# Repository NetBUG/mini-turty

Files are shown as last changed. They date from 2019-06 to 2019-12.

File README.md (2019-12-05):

# mini-turty

ROS package for the Mini-Turty robot.

Original product website: https://www.rhoeby.com/product/mini-turty
    
The Mini-Turty Robot from Rhoeby Dynamics represents a new level of value and functionality in a ROS navigation-capable robot. Designed with the lowest cost and complete user serviceability in mind, this robot is providing greatly improved access to advanced robotics navigation and much more!

## Hardware
The repository contains a [sample platform](mini_turty3/hw/lasercut) designed to be made with laser cutting. 
The base is cut out of 3mm birch plywood with principal strength direction oriented transversely (i.e. robot does not bend between the wheels).
Any other elements are cut out of 3 or 4mm acrylic sheet of any color. Motor holders are not optimal and will be improved soon to provide active suspension.
Unfortunately, the front navigation module (can be seen on sheets as a rectangle of 120x85 mm) was made long ago and design was lost. It contains:
 - Raspberry Pi 3 with heatsink, mounted on 4xM2 screws on the bottom sheet;
 - Neato xv11 lidar, mounted on upper sheet (which is elevated with 30mm M3 screws and pipe-like stands)
 - Raspberry Pi 3 extension made on a prototyping board with PLS connectors, providing connections to
  * lidar through on-board UART (serial kernel logging was disabled)
  * lidar motor power through a low-power SOT23 MOSFET
  * stepper driver outputs
  * I2C connector for  sensors (used for IMU)
  * 4xGPIO pins

The following external components have been used and fit on the base:
 - [18650-sized battery holder](https://www.thingiverse.com/thing:456900)
 - [LV8729 drivers](https://www.aliexpress.com/item/32808950520.html)
 - 2xNEMA17 stepper motors with Makeblocks wheels and wheel hubs
 - A [ball stand](https://pandao.ru/product/233c3d45-5e80-4f82-84e4-e2d594d67a44)

The following components have been fit on the upper board
 - A stepdown module using XL6009 chip
 - An [IMU](https://amperka.ru/product/troyka-imu-10-dof)
 - An IR receiver
 - [Power controller board](mini_turty3/hw/controller)

Drawings use the following coloring convention:
 - black means the lines that have to be cut
 - red means lines denoting mounted parts dimensions and should be omitted when cutting (originally it was used as pale dashed line)
 - yellow originally denoted contours filled with yellow and was used in engraving mode to provide submerged areas to hide PCBs or screen frame

## Things You Can Do With Your Mini-Turty Robot

There are many things you can do with your Mini-Turty robot, including:

- Basics: ROS learning
- Teleop: robot remote control
- Map Building: make maps of your home or office for the robot to use
- Navigation: the robot moves autonomously around your home or office
- Tele-Viewing: see what your robot sees, even from another room*
- Frontier Exploration: the robot autonomously explores unknown terrain*
- Computer Vision: Mini-Turty recognizes objects in its environment*

*Coming soon, to a robot near you!

Available in kit form*, or fully assembled and ready to go. Either way, Mini-Turty provides endless hours of educational fun and represents the ideal platform for learning the Robot Operating System.

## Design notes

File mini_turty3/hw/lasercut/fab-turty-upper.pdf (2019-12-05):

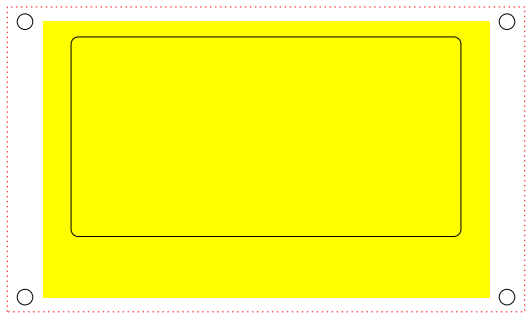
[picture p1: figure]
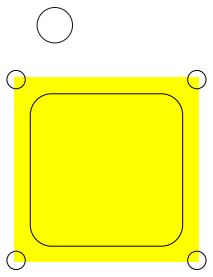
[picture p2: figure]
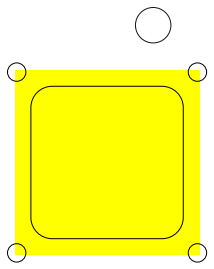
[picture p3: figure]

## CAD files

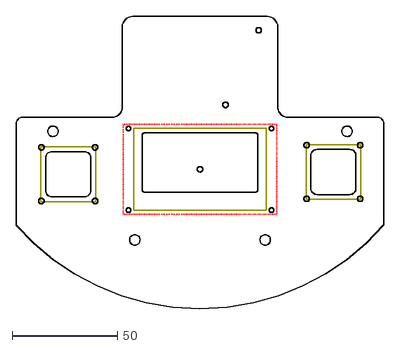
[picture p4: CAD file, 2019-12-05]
mini_turty3/hw/lasercut/fab-turty-upper.dxf
175.0 x 139.0

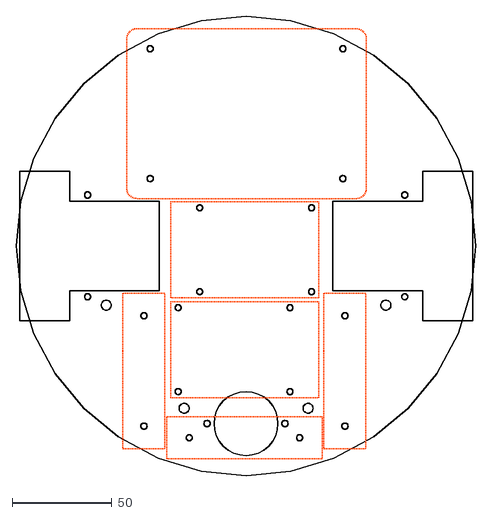
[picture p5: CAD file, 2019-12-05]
mini_turty3/hw/lasercut/fab-turty-base.dxf
230.0 x 230.0

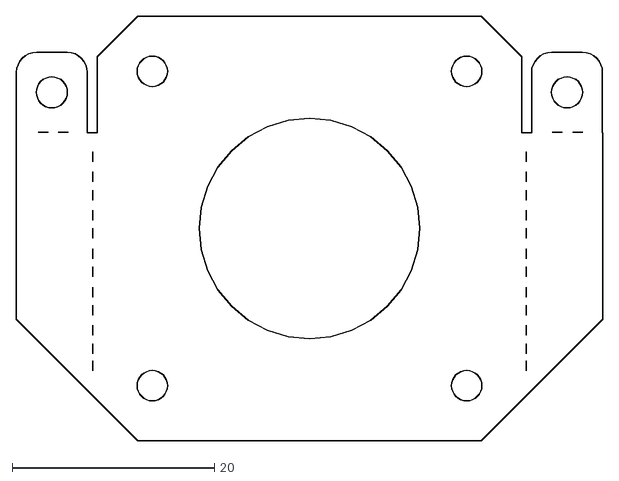
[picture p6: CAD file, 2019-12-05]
mini_turty3/hw/lasercut/fab-turty-motor-holder-x2.dxf
58.0 x 42.0

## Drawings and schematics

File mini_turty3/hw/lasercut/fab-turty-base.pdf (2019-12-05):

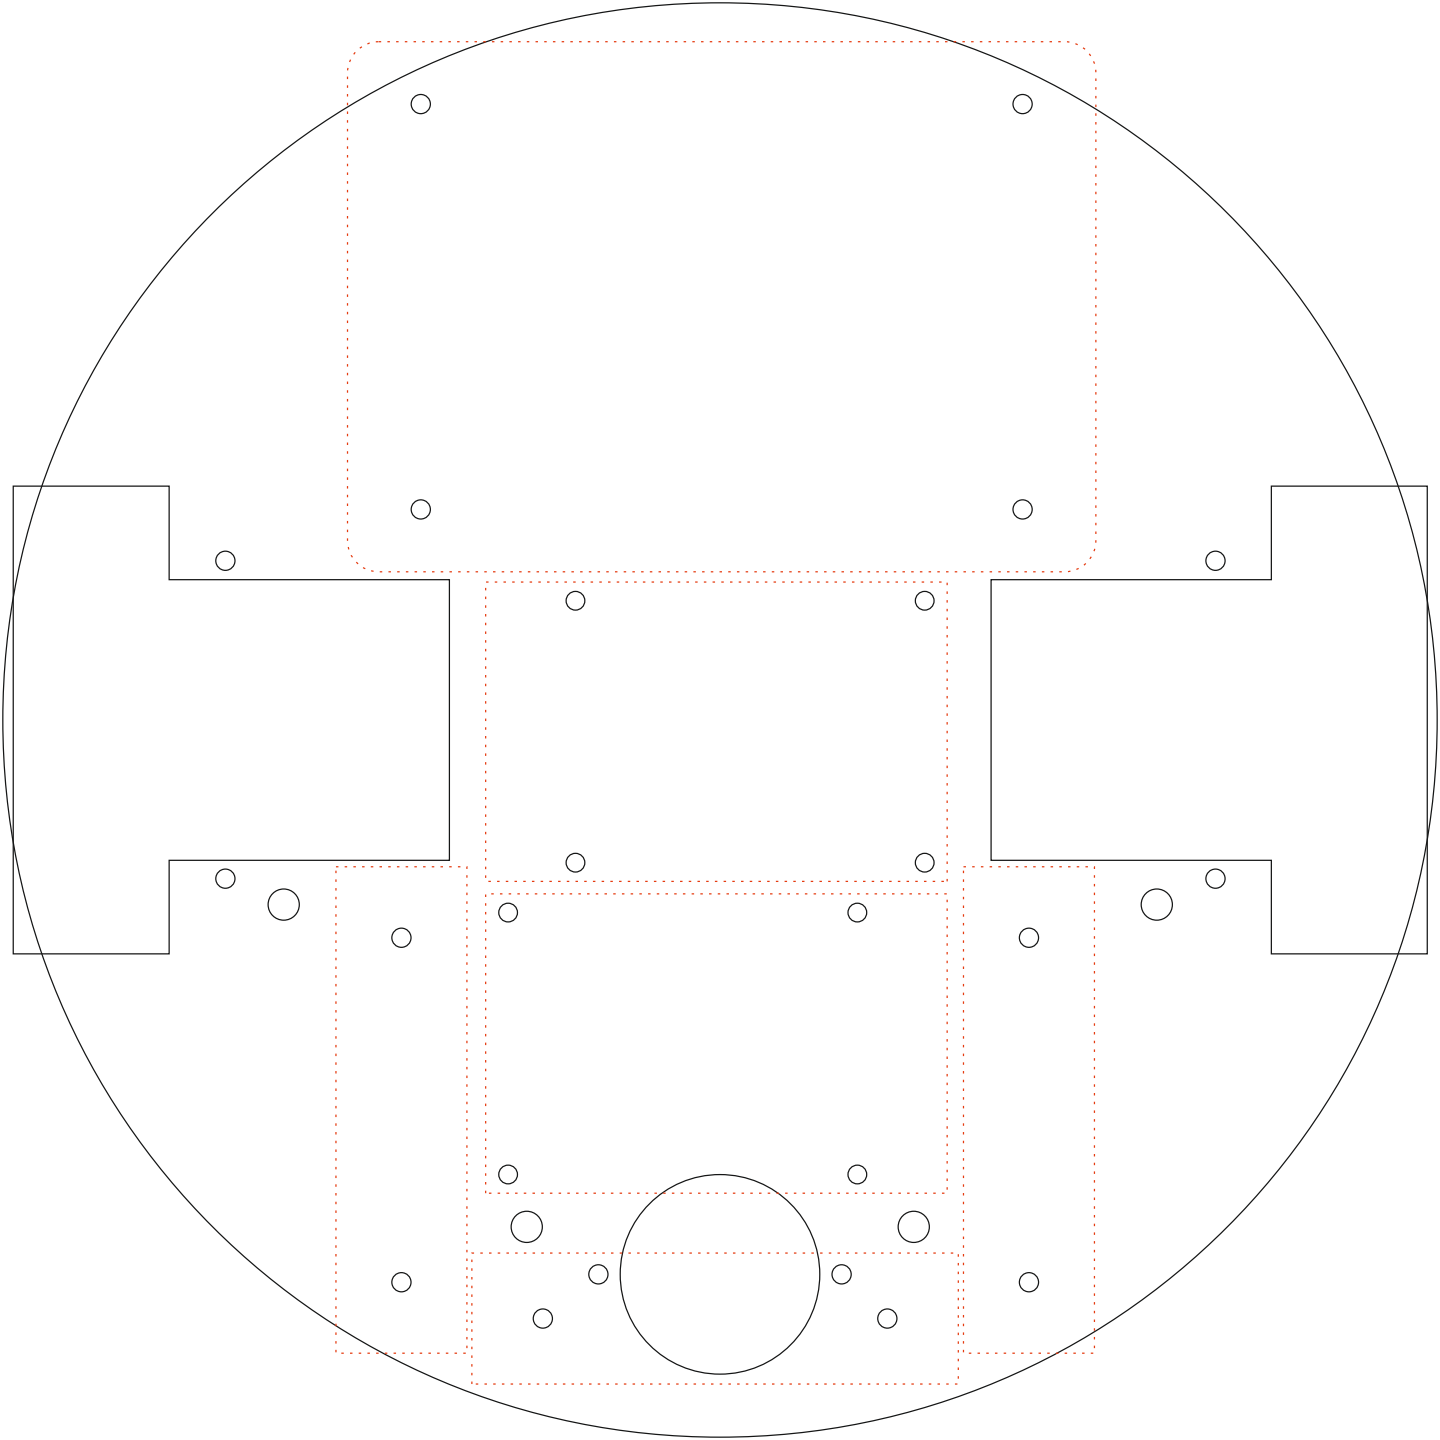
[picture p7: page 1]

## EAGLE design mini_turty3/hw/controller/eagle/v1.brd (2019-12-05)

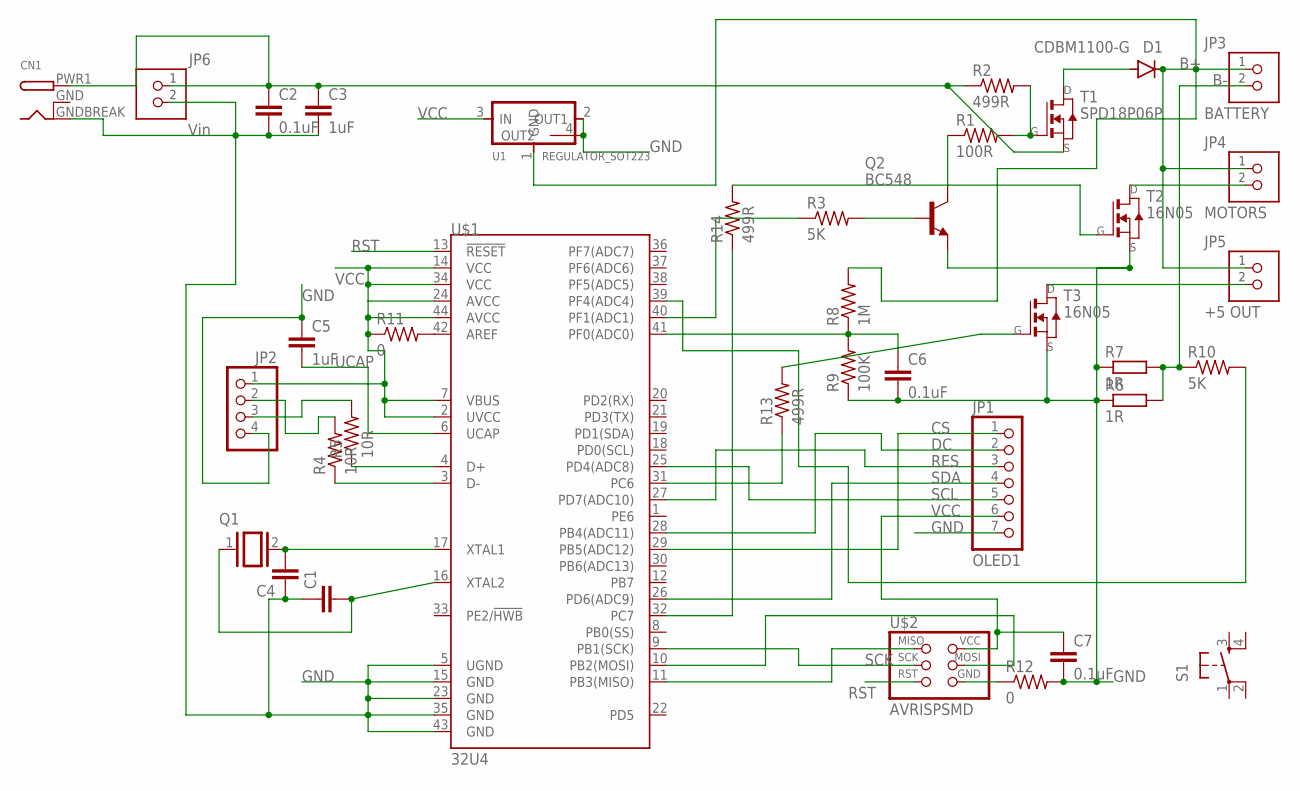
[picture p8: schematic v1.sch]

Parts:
C1, C4: C-EUC1206; C1206
C2, C6, C7: 0.1uF; C1206
C3, C5: 1uF; C1206
CN1: DCBARRELSMT; DCJACK_2MM_SMT
D1: CDBM1100-G; MINI-SMA
JP1: OLED1; 1X07
JP2: PINHD-1X4; 1X04
JP3: BATTERY; ED555DS-2DS
JP4: MOTORS; ED555DS-2DS
JP5: +5 OUT; ED555DS-2DS
JP6: Vin; ED555DS-2DS
Q1: XTAL/S; QS
Q2: BC548; TO92-EBC
R1: 100R; M1206
R2, R13, R14: 499R; M1206
R3, R10: 5K; M1206
R4, R5: 10R; M1206
R6, R7: 1R; R6332W
R8: 1M; M1206
R9: 100K; M1206
R11, R12: 0; M1206
S1: 6MM_SWITCH6MM_SWITCH; 6MM_SWITCH
T1: SPD18P06P; TO252
T2, T3: 16N05; TO252
U1: REGULATOR_SOT223; SOT223
U$1: 32U4; TQFP44
U$2: AVRISPSMD; 2X03SMD

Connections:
B+: D1.KATHODE, JP3.1, JP4.1, JP5.1, R8.2, U1.1 (GND)
B-: JP3.2, R6.2, R7.2, R10.1
CS: JP1.1, U$1.29 (PB5(ADC12))
DC: JP1.2, U$1.28 (PB4(ADC11))
GND: C1.1, C2.2, C3.2, C4.1, C5.1, C6.2, C7.2, CN1.GNDBREAK (GND), JP1.7, JP2.4, JP6.2, Q2.E, R6.1, R7.1, R9.1, R12.2, T2.2 (S), T3.2 (S), U1.2 (OUT1), U1.4 (OUT2), U$1.5 (UGND), U$1.15 (GND), U$1.23 (GND), U$1.35 (GND), U$1.43 (GND)
GNDBREAK: CN1.GND (GNDBREAK)
MISO: U$1.11 (PB3(MISO)), U$2.1 (MISO)
MOSI: U$1.10 (PB2(MOSI)), U$2.4 (MOSI)
unnamed: C4.2, Q1.2, U$1.17 (XTAL1)
unnamed: R11.2, U$1.42 (AREF)
unnamed: R3.1, U$1.40 (PF1(ADC1))
unnamed: R12.1, U$2.6 (GND)
unnamed: C1.2, Q1.1, U$1.16 (XTAL2)
unnamed: JP5.2, T3.3 (D)
unnamed: JP4.2, T2.3 (D)
unnamed: R14.1, U$1.32 (PC7)
unnamed: D1.ANODE, T1.3 (D)
unnamed: R1.2, R2.2, T1.1 (G)
unnamed: Q2.C, R1.1
unnamed: Q2.B, R3.2
unnamed: R13.1, U$1.31 (PC6)
unnamed: C6.1, R8.1, R9.2, U$1.41 (PF0(ADC0))
unnamed: R10.2, U$1.39 (PF4(ADC4))
unnamed: JP2.3, R5.2
unnamed: R5.1, U$1.4 (D+)
unnamed: R4.1, U$1.3 (D-)
unnamed: JP2.2, R4.2
unnamed: R14.2, T2.1 (G)
unnamed: R13.2, T3.1 (G)
RES: JP1.3, U$1.27 (PD7(ADC10))
RST: U$1.13 (!RESET), U$2.5 (RST)
SCK: U$1.9 (PB1(SCK)), U$2.3 (SCK)
SCL: JP1.5, U$1.25 (PD4(ADC8))
SDA: JP1.4, U$1.26 (PD6(ADC9))
UCAP: C5.2, U$1.6 (UCAP)
VCC: C7.1, JP1.6, JP2.1, R11.1, U1.3 (IN), U$1.2 (UVCC), U$1.7 (VBUS), U$1.14 (VCC), U$1.24 (AVCC), U$1.34 (VCC), U$1.44 (AVCC), U$2.2 (VCC)
VIN: C2.1, C3.1, CN1.PWR1 (PWR), JP6.1, R2.1, T1.2 (S)

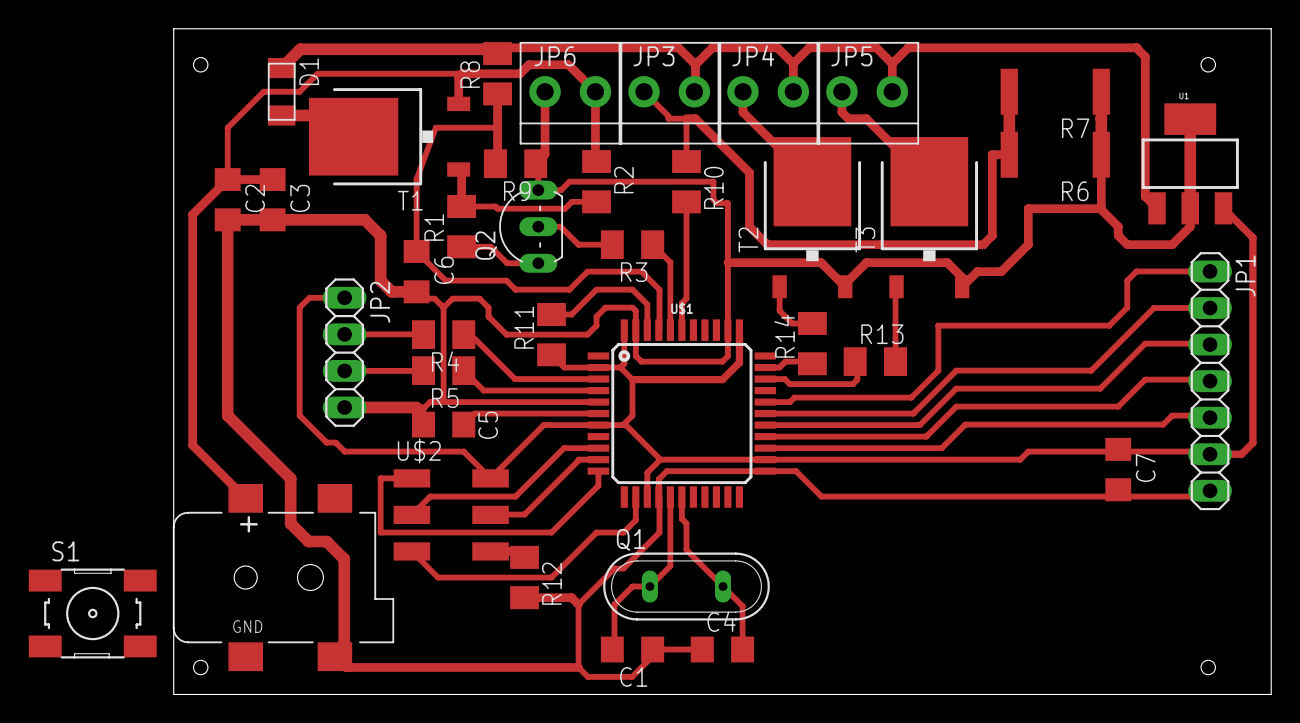
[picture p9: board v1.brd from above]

Board: 2 copper layers, 76.2 x 46.2 mm, 38 parts (0 on the bottom side), 36 nets.

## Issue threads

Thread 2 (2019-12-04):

Олег, выложи механику

kotenev, 2019-12-04:
Приветствую. По договорённости в чате "ros meetup 2019" создал этот issue :-)

NetBUG, 2019-12-05:
Вспомнил, что у меня есть удалённый доступ))
Выложил в ветку `hw`, в подкаталог `mini-turty3/hw`.
Фотографии, чертёж модуля с RPi и лидаром, полноценную прошивку BMS выложу, когда приеду в Москву.
Привод с ременной передачей и подвеской, видимо, в январе.

Closed 2019-12-05.

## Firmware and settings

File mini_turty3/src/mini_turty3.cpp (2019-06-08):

#include <stdio.h>
#include <stdlib.h>
#include <signal.h>
#include <string>

#include <fcntl.h>
#include <termios.h>
#include <sys/select.h>

#include "pigpiod_if2.h"
#include "ros/ros.h"
#include <ros/console.h>
#include "nav_msgs/Odometry.h"
#include "tf/transform_broadcaster.h"

/*
NOTE - Must start 'pigpiod' daemon first:
  sudo pigpiod
*/

// options
#define MINI_USE_CONSOLE 1

// GPIO pin assignments
#define GPIO_SLEEP 16
#define GPIO_STEP1 19
#define GPIO_DIR1  26
#define GPIO_STEP0 13
#define GPIO_DIR0  20

#define MOTOR_SPEED_SLEW_SIZE 0.45 // rate of change of motor speed (in m/s)
#define MAX_DEFAULT_SPEED 16

typedef enum DIFFDRIVE_MOTOR
{
  DIFFDRIVE_MOTOR_LEFT,
  DIFFDRIVE_MOTOR_RIGHT,
  DIFFDRIVE_MOTOR_MAX
} DIFFDRIVE_MOTOR;

typedef struct Motor_t {
  double currentSpeed;
  double targetSpeed;
} Motor_t;

class MiniTurtyBase
{
  public:
    MiniTurtyBase(int the_pi, float max_speed);
    virtual ~MiniTurtyBase() {};

    void setEnableOdomTransform(const bool enabled);
    void setCmdVelTopic(const std::string topic_name);
    void setMotorSpeed(DIFFDRIVE_MOTOR motor_num, double speed);

  protected:
    void cmdVelCallback(const geometry_msgs::Twist::ConstPtr& twist);
    void timerCallback(const ros::TimerEvent&);
    void updateMotorControl(DIFFDRIVE_MOTOR motor_num);
    void publishOdom(const double vx, const double vth);

  private:
    int pi;
    float max_speed;
    ros::NodeHandle node;
    ros::Subscriber cmd_vel_sub;
    ros::Timer timer;
    Motor_t motors[DIFFDRIVE_MOTOR_MAX];
    tf::TransformBroadcaster odom_broadcaster;
    bool odomTransformEnabled;
};

int init_gpio(void);

#if MINI_USE_CONSOLE
void consoleSetTerminalMode(void);
char processConsole(MiniTurtyBase *mini);
#else
void sig_handler(int s);
static bool got_ctrl_c = false;
#endif

//////////////////////////////////////////////////////////////////////////////

int main(int argc, char *argv[])
{
  int pi;
  
  ROS_WARN("Hello!\n");

  pi = init_gpio();
  if(pi) {
    ROS_ERROR("Error initializing pigpio!\n");
    return pi;
  }

  ros::init(argc, argv, "mini_turty");

#if MINI_USE_CONSOLE
  consoleSetTerminalMode();
#else
  signal(SIGINT, sig_handler);
#endif

  ros::NodeHandle private_node_handle_("~");
  ros::Rate loop_rate(10);

  int enable_odom_transform;
  float max_speed;
  private_node_handle_.param("enable_odom_transform", enable_odom_transform, int(1));
  private_node_handle_.param("max_speed", max_speed, float(MAX_DEFAULT_SPEED));

  MiniTurtyBase mini(pi, max_speed);
  mini.setCmdVelTopic("cmd_vel");
  mini.setEnableOdomTransform(enable_odom_transform);
  mini.setEnableOdomTransform(enable_odom_transform);

  while (ros::ok()) 
  {
#if MINI_USE_CONSOLE
    if(processConsole(&mini) == 'q') {
      ROS_WARN("Got 'q'");
      break;
    }
#else
    if (got_ctrl_c) {
      ROS_WARN("Got Ctrl-C");
      break;
    }
#endif

    ros::spinOnce();
    loop_rate.sleep();
  }

  // set SLEEP (active low)
  gpio_write(pi, GPIO_SLEEP, 1);
  
  pigpio_stop(pi);

  ROS_WARN("Exiting.");

  exit(0);
}

/////////////////////////////////////////////////////////////////////////

/*---------------------------------------------------------------------
 *
 *---------------------------------------------------------------------*/
MiniTurtyBase::MiniTurtyBase(int the_pi, float max_speed)
{
  pi = the_pi;

  motors[DIFFDRIVE_MOTOR_LEFT].currentSpeed = 0;
  motors[DIFFDRIVE_MOTOR_RIGHT].currentSpeed = 0;
  motors[DIFFDRIVE_MOTOR_LEFT].targetSpeed = 0;
  motors[DIFFDRIVE_MOTOR_RIGHT].targetSpeed = 0;

  timer = node.createTimer(ros::Duration(0.05), &MiniTurtyBase::timerCallback, this);
}

/*---------------------------------------------------------------------
 *
 *---------------------------------------------------------------------*/
void MiniTurtyBase::timerCallback(const ros::TimerEvent&)
{
  double vx;
  double vth;
  
  updateMotorControl(DIFFDRIVE_MOTOR_LEFT);
  updateMotorControl(DIFFDRIVE_MOTOR_RIGHT);

  vx = (motors[DIFFDRIVE_MOTOR_RIGHT].currentSpeed + 
        motors[DIFFDRIVE_MOTOR_LEFT].currentSpeed) / 2;
//  vth = (motors[DIFFDRIVE_MOTOR_RIGHT].currentSpeed - 
//         motors[DIFFDRIVE_MOTOR_LEFT].currentSpeed) * 8.25;
//  vth = (motors[DIFFDRIVE_MOTOR_RIGHT].currentSpeed - 
//         motors[DIFFDRIVE_MOTOR_LEFT].currentSpeed) * 4;
  vth = (motors[DIFFDRIVE_MOTOR_RIGHT].currentSpeed - 
         motors[DIFFDRIVE_MOTOR_LEFT].currentSpeed) * 8;

  // TODO: add a second param to control this rather than hijacking odom *transform* enable
  // don't publish odom when running hector!
  if(odomTransformEnabled)
    publishOdom(vx, vth);
}

/*---------------------------------------------------------------------
 *
 *---------------------------------------------------------------------*/
void MiniTurtyBase::updateMotorControl(DIFFDRIVE_MOTOR motor_num)
{
  double currentSpeed = motors[motor_num].currentSpeed;
  double targetSpeed = motors[motor_num].targetSpeed;
  
  if(currentSpeed == targetSpeed) return;

  // slew the current speed toward the target speed
  if(currentSpeed < targetSpeed) {
    if(currentSpeed+MOTOR_SPEED_SLEW_SIZE > targetSpeed)
      currentSpeed = targetSpeed;
    else
      currentSpeed += MOTOR_SPEED_SLEW_SIZE;
  }
  else if (currentSpeed > targetSpeed) {
    if(currentSpeed-MOTOR_SPEED_SLEW_SIZE < targetSpeed)
      currentSpeed = targetSpeed;
    else
      currentSpeed -= MOTOR_SPEED_SLEW_SIZE;
  }

  // write the current speed and direction to the motor control
  switch(motor_num) 
  {
  case DIFFDRIVE_MOTOR_LEFT:
    if(currentSpeed < 0) 
      gpio_write(pi, GPIO_DIR1, 0); // set DIRECTION
    else
      gpio_write(pi, GPIO_DIR1, 1);
//    hardware_PWM(pi, GPIO_STEP1, abs((int16_t)(currentSpeed*1000.0)), 500000);
    hardware_PWM(pi, GPIO_STEP1, abs((int16_t)(currentSpeed*2000.0)), 500000);
    break;
  case DIFFDRIVE_MOTOR_RIGHT:
    if(currentSpeed < 0) 
      gpio_write(pi, GPIO_DIR0, 1); // set DIRECTION
    else
      gpio_write(pi, GPIO_DIR0, 0);
//    hardware_PWM(pi, GPIO_STEP0, abs((int16_t)(currentSpeed*1000.0)), 500000);
    hardware_PWM(pi, GPIO_STEP0, abs((int16_t)(currentSpeed*2000.0)), 500000);
    break;
  }

  motors[motor_num].currentSpeed = currentSpeed;

  // set/reset the SLEEP of the motor control
#if 0
  if(abs(motors[DIFFDRIVE_MOTOR_LEFT].currentSpeed) < MOTOR_SPEED_SLEW_SIZE && 
     abs(motors[DIFFDRIVE_MOTOR_RIGHT].currentSpeed) < MOTOR_SPEED_SLEW_SIZE)
#else
  if(motors[DIFFDRIVE_MOTOR_LEFT].currentSpeed == 0 && 
     motors[DIFFDRIVE_MOTOR_RIGHT].currentSpeed == 0)
#endif
    gpio_write(pi, GPIO_SLEEP, 1); // set SLEEP (active low)
  else
    gpio_write(pi, GPIO_SLEEP, 0);

#if 0
  ROS_WARN("Motor: %d, Current speed: %f, Target speed: %f", 
           motor_num, currentSpeed, targetSpeed);
#endif
}

// JJ - provide odom transform
#if 1
/*----------------------------------------------------------
 * setEnableOdomTransform() - enable the odom transform
 *--------------------------------------------------------*/
void MiniTurtyBase::setEnableOdomTransform(const bool enabled)
{
  odomTransformEnabled = enabled;
}
#endif

/*----------------------------------------------------------
 * publishOdom() - publish odom data 
 *--------------------------------------------------------*/
void MiniTurtyBase::publishOdom(const double vx, const double vth)
{
  double vy = 0;
  static double x = 0;
  static double y = 0;
  static double th = 0;
  ros::Time current_time = ros::Time::now();
  static ros::Time last_time = current_time;
  static ros::Publisher odom_pub = node.advertise<nav_msgs::Odometry>("odom", 50);

#if 1
  ROS_INFO("odom vx: %f, vy: %f, vth: %f\r", vx, vy, vth);
//  printf("odom vx: %f, vy: %f, vth: %f\n", vx, vy, vth);
#endif

  // compute odometry in a typical way given the velocities of the robot
  double dt = (current_time - last_time).toSec();
  double delta_x = (vx * cos(th) - vy * sin(th)) * dt;
  double delta_y = (vx * sin(th) + vy * cos(th)) * dt;
  double delta_th = vth * dt;

  // integrate to track position
  x += delta_x;
  y += delta_y;
  th += delta_th;

  // since all odometry is 6DOF we'll need a quaternion created from yaw
  geometry_msgs::Quaternion odom_quat = tf::createQuaternionMsgFromYaw(th);

  // send the odom-->base_footprint transform: only if NOT using robot_pose_ekf!
  geometry_msgs::TransformStamped odom_trans;
  odom_trans.header.stamp = current_time;
//    odom_trans.header.frame_id = "odom_combined";
  odom_trans.header.frame_id = "odom";
//    odom_trans.child_frame_id = "base_link";
  odom_trans.child_frame_id = "base_footprint";
  odom_trans.transform.translation.x = x;
  odom_trans.transform.translation.y = y;
  odom_trans.transform.translation.z = 0.0;
  odom_trans.transform.rotation = odom_quat;
  odom_broadcaster.sendTransform(odom_trans);
#if 0
  ROS_INFO("odom x: %f, y: %f, z-rot: %f", x, y, th);
#endif

  // publish the odometry message
  nav_msgs::Odometry odom;
  odom.header.stamp = current_time;
//  odom.header.frame_id = "odom_combined";
  odom.header.frame_id = "odom";
  odom.child_frame_id = "base_footprint";

  // set the position and orientation
  odom.pose.pose.position.x = x;
  odom.pose.pose.position.y = y;
  odom.pose.pose.position.z = 0.0;
  odom.pose.pose.orientation = odom_quat;

  // TODO: these were repurposed from nxt_ros:: base_odometry.py, check the validity
  odom.pose.covariance[0] = 0.00001;    // x - are all these correct?
  odom.pose.covariance[7] = 0.00001;    // y
  odom.pose.covariance[14] = 10;    // z (set high because robot does not move up/down?)
  odom.pose.covariance[21] = 1;   // rot x
  odom.pose.covariance[28] = 1;   // rot y
  odom.pose.covariance[35] = 1;   // rot z

  // set the velocity
  odom.twist.twist.linear.x = vx;
  odom.twist.twist.linear.y = vy;
  odom.twist.twist.angular.z = vth;

  last_time = current_time;

  // publish the odom message
  odom_pub.publish(odom);
}

/*----------------------------------------------------------
 * setCmdVelTopic() - set the cmd_vel topic name 
 *--------------------------------------------------------*/
void MiniTurtyBase::setCmdVelTopic(const std::string topic_name)
{
  cmd_vel_sub = node.subscribe(topic_name, 100, &MiniTurtyBase::cmdVelCallback, this);
}

/*----------------------------------------------------------
 * cmdVelCallback()
 *--------------------------------------------------------*/
void MiniTurtyBase::cmdVelCallback(const geometry_msgs::Twist::ConstPtr& twist)
{
//  motors[DIFFDRIVE_MOTOR_LEFT].targetSpeed = twist->linear.x-twist->angular.z;
//  motors[DIFFDRIVE_MOTOR_RIGHT].targetSpeed = twist->linear.x+twist->angular.z;
//  motors[DIFFDRIVE_MOTOR_LEFT].targetSpeed = twist->linear.x-(twist->angular.z/8.25);
//  motors[DIFFDRIVE_MOTOR_RIGHT].targetSpeed = twist->linear.x+(twist->angular.z/8.25);
  motors[DIFFDRIVE_MOTOR_LEFT].targetSpeed = twist->linear.x-(twist->angular.z/16);
  motors[DIFFDRIVE_MOTOR_RIGHT].targetSpeed = twist->linear.x+(twist->angular.z/16);

#if 1
  ROS_WARN("twist linear.x: %f, y: %f, angular.z: %f\r", 
            twist->linear.x, twist->linear.y, twist->angular.z);  
#endif
}

void MiniTurtyBase::setMotorSpeed(DIFFDRIVE_MOTOR motor_num, double speed)
{
  motors[motor_num].targetSpeed = speed;
}

/////////////////////////////////////////////////////////////////////////

#if !MINI_USE_CONSOLE
void sig_handler(int s)
{
  if (s == 2) {
    got_ctrl_c = true; 
  }
}
#endif

int init_gpio(void)
{
  int pi = pigpio_start(NULL, NULL);
  if (pi < 0) goto error;

  set_mode(pi, GPIO_SLEEP, PI_OUTPUT);
  set_mode(pi, GPIO_DIR0, PI_OUTPUT);
  set_mode(pi, GPIO_DIR1, PI_OUTPUT);
  set_mode(pi, GPIO_STEP0, PI_OUTPUT);
  set_mode(pi, GPIO_STEP1, PI_OUTPUT);

error:
  return pi;
}

/*---------------------------------------------------------------
 * console functions 
 *-------------------------------------------------------------*/

#if MINI_USE_CONSOLE
struct termios orig_termios;

void consoleResetTerminalMode();
int consoleKbHit();
int consoleGetCh();

static bool started = true;
static double left_motor_speed = 0;
static double right_motor_speed = 0;

char processConsole(MiniTurtyBase *mini)
{
  char kbd_ch = 0;
  int i;
// JJ - add theta trim command
#if 0
  static int thetaTrim = 0;
#endif

  if (consoleKbHit())
  {
    kbd_ch = consoleGetCh();
    
    switch (kbd_ch)
    {
    case 'b':
      if (left_motor_speed > 0 && left_motor_speed < 4) left_motor_speed = 4;
      if (right_motor_speed > 0 && right_motor_speed < 4) right_motor_speed = 4;
      left_motor_speed -= 4;
      right_motor_speed -= 4;
      mini->setMotorSpeed(DIFFDRIVE_MOTOR_LEFT, left_motor_speed);
      mini->setMotorSpeed(DIFFDRIVE_MOTOR_RIGHT, right_motor_speed);
      ROS_INFO("Got BWD\n");
      break;
    case 0x42:
      left_motor_speed -= 0.25;
      right_motor_speed -= 0.25;
      mini->setMotorSpeed(DIFFDRIVE_MOTOR_LEFT, left_motor_speed);
      mini->setMotorSpeed(DIFFDRIVE_MOTOR_RIGHT, right_motor_speed);
      ROS_INFO("Got BWD\n");
      break;
    case 'f':
      left_motor_speed += 4;
      right_motor_speed += 4;
      mini->setMotorSpeed(DIFFDRIVE_MOTOR_LEFT, left_motor_speed);
      mini->setMotorSpeed(DIFFDRIVE_MOTOR_RIGHT, right_motor_speed);
      ROS_INFO("Got FWD\n");
      break;
    case 0x41:
      left_motor_speed += 0.25;
      right_motor_speed += 0.25;
      mini->setMotorSpeed(DIFFDRIVE_MOTOR_LEFT, left_motor_speed);
      mini->setMotorSpeed(DIFFDRIVE_MOTOR_RIGHT, right_motor_speed);
      ROS_INFO("Got FWD\n");
      break;
    case 'l':
    case 0x44:
#if false
      left_motor_speed -= 0.025;
      right_motor_speed += 0.025;
#else
      left_motor_speed -= 0.05;
      right_motor_speed += 0.05;
#endif
      mini->setMotorSpeed(DIFFDRIVE_MOTOR_LEFT, left_motor_speed);
      mini->setMotorSpeed(DIFFDRIVE_MOTOR_RIGHT, right_motor_speed);
      ROS_INFO("Got LEFT\n");
      break;
    case 'r':
    case 0x43:
#if false
      left_motor_speed += 0.025;
      right_motor_speed -= 0.025;
#else
      left_motor_speed += 0.05;
      right_motor_speed -= 0.05;
#endif
      mini->setMotorSpeed(DIFFDRIVE_MOTOR_LEFT, left_motor_speed);
      mini->setMotorSpeed(DIFFDRIVE_MOTOR_RIGHT, right_motor_speed);
      ROS_INFO("Got RIGHT\n");
      break;
    case 's':
      left_motor_speed = 0.0;
      right_motor_speed = 0.0;
      mini->setMotorSpeed(DIFFDRIVE_MOTOR_LEFT, left_motor_speed);
      mini->setMotorSpeed(DIFFDRIVE_MOTOR_RIGHT, right_motor_speed);
      ROS_INFO("Got STOP\n");
      break;

      // JJ - add theta trim command
#if 0
    case '+':
      if (pScanner->theta_trim_ < 128) {
        pScanner->theta_trim_ += 1;
      }
      pScanner->dxlSetThetaTrim(pScanner->theta_trim_);
      break;
    case '-':
      if (pScanner->theta_trim_ > -128) {
        pScanner->theta_trim_ -= 1;
      }
      pScanner->dxlSetThetaTrim(pScanner->theta_trim_);
      break;
#endif
    default:
      break;
    }
  }

  return kbd_ch;
}

void consoleResetTerminalMode()
{
  tcsetattr(0, TCSANOW, &orig_termios);
}

void consoleSetTerminalMode()
{
  struct termios new_termios;

  /* take two copies - one for now, one for later */
  tcgetattr(0, &orig_termios);
  memcpy(&new_termios, &orig_termios, sizeof(new_termios));

  /* register cleanup handler, and set the new terminal mode */
  atexit(consoleResetTerminalMode);

  cfmakeraw(&new_termios);

  new_termios.c_oflag |= OPOST;

  tcsetattr(0, TCSANOW, &new_termios);
}

int consoleKbHit()
{
  struct timeval tv = { 0L, 0L};

  fd_set fds;
  FD_ZERO(&fds);
  FD_SET(0, &fds);
  return select(1, &fds, NULL, NULL, &tv);
}

int consoleGetCh()
{
  int r;
  unsigned char c;
  if ((r = read(0, &c, sizeof(c))) < 0)
  {
    return r;
  }
  else
  {
    return c;
  }
}
#endif

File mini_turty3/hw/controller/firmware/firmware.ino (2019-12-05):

#include "U8glib.h"

#define PIN_D0   4
#define PIN_D1   12
#define PIN_RES  9
#define PIN_DC   8
#define PIN_CS   6
#define PIN_BAT  A5

U8GLIB_SSD1306_128X64 u8g(PIN_D0, PIN_D1, PIN_RES, PIN_DC, PIN_CS);
// U8G2_SSD1309_128X64_NONAME0_1_4W_SW_SPI u8g(PIN_D0, PIN_D1, PIN_RES, PIN_DC, PIN_CS);  // SW SPI Com: SCK = 4, MOSI = 5, CS = 6, A0 = 7 (new white HalTec OLED)
// U8GLIB_SSD1306_128X64 u8g(0);
// U8G2_SSD1306_128X64_NONAME_2_SW_I2C u8g(U8G2_R0, PIN_D0, PIN_D1);

char out[6];  // текстовый массив
long ms = 0;
long ms1 = 0;
bool bArm = true;

#define fablab_width 64
#define fablab_height 59
const static unsigned char fablab_bits[] U8G_PROGMEM = {
   0xff, 0xff, 0xff, 0xff, 0xff, 0xff, 0xff, 0xff, 0xff, 0xff, 0xff, 0xff,
   0xff, 0xff, 0xff, 0xff, 0xff, 0xff, 0xff, 0xff, 0xff, 0xff, 0xff, 0xff,
   0xf7, 0xff, 0xff, 0xff, 0xff, 0xff, 0xff, 0xff, 0xc7, 0xff, 0xff, 0xff,
   0xff, 0xff, 0x9f, 0xff, 0x87, 0xff, 0xff, 0xff, 0xff, 0xff, 0x07, 0xff,
   0x07, 0xfe, 0xff, 0xff, 0xff, 0xff, 0x01, 0xff, 0x07, 0xfc, 0xff, 0xff,
   0xff, 0xff, 0x10, 0xff, 0xc7, 0xfc, 0xff, 0xff, 0xff, 0xff, 0x98, 0xff,
   0xc7, 0xff, 0xff, 0xff, 0xff, 0xff, 0x88, 0xff, 0x07, 0xff, 0xff, 0xff,
   0xff, 0xff, 0x00, 0xff, 0x07, 0xfc, 0xff, 0xff, 0xff, 0xff, 0x00, 0xff,
   0x47, 0xfc, 0xff, 0xff, 0xff, 0xff, 0x18, 0xff, 0xc7, 0xfd, 0xff, 0xff,
   0xff, 0xff, 0x99, 0xff, 0xc7, 0xff, 0xff, 0xff, 0xff, 0xff, 0x81, 0xff,
   0xcf, 0xff, 0xff, 0xff, 0xff, 0xff, 0xc1, 0xff, 0xff, 0xff, 0xff, 0xff,
   0xff, 0xff, 0xe1, 0xff, 0xff, 0xff, 0xff, 0xff, 0xff, 0xff, 0xf9, 0xff,
   0xff, 0xff, 0xff, 0xcf, 0xff, 0xff, 0xff, 0xff, 0xff, 0xff, 0xff, 0x8f,
   0xff, 0xff, 0xff, 0xff, 0xff, 0xff, 0xff, 0x87, 0xff, 0xff, 0xff, 0xff,
   0xff, 0xff, 0xff, 0x87, 0xff, 0xff, 0xff, 0xff, 0xff, 0xff, 0xff, 0x03,
   0xff, 0xff, 0xff, 0xff, 0xff, 0xff, 0xff, 0x03, 0xff, 0xff, 0xff, 0xff,
   0xff, 0xff, 0xff, 0x23, 0xff, 0xff, 0xff, 0xff, 0xff, 0xff, 0xff, 0x21,
   0xff, 0xff, 0xff, 0xff, 0xff, 0xff, 0xff, 0x01, 0xfe, 0xff, 0xff, 0xff,
   0xff, 0xff, 0xff, 0x01, 0xfe, 0xff, 0xff, 0xff, 0xff, 0xff, 0xff, 0x3f,
   0xfe, 0xff, 0xff, 0xff, 0xff, 0xff, 0xff, 0x7f, 0xfc, 0xff, 0xfe, 0xff,
   0xff, 0xff, 0xff, 0x7f, 0xfc, 0xff, 0xf8, 0xff, 0xff, 0xff, 0xff, 0xff,
   0xfc, 0xff, 0xe0, 0xff, 0xcf, 0xff, 0xff, 0xff, 0xff, 0xff, 0xc0, 0xff,
   0xc7, 0xff, 0xff, 0xff, 0xff, 0xff, 0x8c, 0xff, 0xc7, 0xff, 0xff, 0xff,
   0xff, 0xff, 0x9c, 0xff, 0xc7, 0xff, 0xff, 0xff, 0xff, 0xff, 0x90, 0xff,
   0xc7, 0xff, 0xff, 0xff, 0xff, 0xff, 0x00, 0xff, 0xc7, 0xf7, 0xff, 0xff,
   0xff, 0xff, 0x80, 0xff, 0xc7, 0xf1, 0xff, 0xff, 0xff, 0xff, 0x8c, 0xff,
   0x07, 0xf0, 0xff, 0xff, 0xff, 0xff, 0x98, 0xff, 0x07, 0xf8, 0xff, 0xff,
   0xff, 0xff, 0x00, 0xff, 0x07, 0xfe, 0xff, 0xff, 0xff, 0xff, 0x03, 0xff,
   0x87, 0xff, 0xff, 0xff, 0xff, 0xff, 0x07, 0xff, 0xc7, 0xff, 0xff, 0xff,
   0xff, 0xff, 0xff, 0xff, 0xf7, 0xff, 0xf7, 0xff, 0xff, 0xff, 0xff, 0xff,
   0xff, 0xff, 0xf8, 0xff, 0xff, 0xff, 0xff, 0xff, 0xff, 0x7f, 0xf8, 0xff,
   0xff, 0xff, 0xff, 0xff, 0xff, 0x3f, 0xfc, 0xff, 0xff, 0xff, 0xff, 0xff,
   0xff, 0x2f, 0xff, 0xff, 0xff, 0xff, 0xff, 0xff, 0xff, 0xb3, 0xff, 0xff,
   0xff, 0xff, 0xff, 0xff, 0xff, 0xe1, 0xff, 0xff, 0xff, 0xff, 0xff, 0xff,
   0x5f, 0xfa, 0xff, 0xff, 0xff, 0xff, 0xff, 0xff, 0x07, 0xfc, 0xff, 0xff,
   0xff, 0xff, 0xff, 0xff, 0x47, 0xff, 0xff, 0xff, 0xff, 0xff, 0xff, 0xff,
   0xc7, 0xff, 0xff, 0xff, 0xff, 0xff, 0xff, 0xff, 0xf7, 0xff, 0xff, 0xff,
   0xff, 0xff, 0xff, 0xff, 0xff, 0xff, 0xff, 0xff, 0xff, 0xff, 0xff, 0xff,
   0xff, 0xff, 0xff, 0xff, 0xff, 0xff, 0xff, 0xff, 0xff, 0xff, 0xff, 0xff,
   0xff, 0xff, 0xff, 0xff };
   
void drawLogo(uint8_t d)
{
    /*u8g.setFont(u8g_font_gdr25r);
    u8g.drawStr(0+d, 30+d, "U");
    u8g.setFont(u8g_font_gdr30n);
    u8g.drawStr90(23+d,10+d,"8");
    u8g.setFont(u8g_font_gdr25r);
    u8g.drawStr(53+d,30+d,"g");
    
    u8g.drawHLine(2+d, 35+d, 47);
    u8g.drawVLine(45+d, 32+d, 12);*/
    //u8g.drawBox(g*w + b*w*8, r*h, w, h);
}

void drawURL(void)
{
  u8g.setFont(u8g_font_profont12);
  u8g.drawStr(1,54,"     fabbot-mate");
  u8g.drawStr(1,64,"   robot offline ;(");
  u8g.drawHLine(1, 43, 127);
}

void drawStatus(bool armed) {
  for (int i=0; i<7; i++) {out[i]=' ';}  // заполнение пробелами 
  // Battery
  int rawBat = analogRead(PIN_BAT);
  int bat = rawBat / 3 * 2;
  u8g.drawVLine(80, 0, 18);
  u8g.drawHLine(80, 17, 48);
  u8g.setColorIndex(0);
  u8g.drawBox(81, 0, 48, 16);
  u8g.setColorIndex(1);
  u8g.setFont(u8g_font_helvB14);
  itoa(bat, out, 10);
  int lastChar = strlen(out);
  out[lastChar + 2] = out[lastChar];
  out[lastChar] = out[lastChar - 1];
  out[lastChar - 1] = '.';
  out[lastChar + 1] = 'v';
  u8g.drawStr(82, 16, out);
  //Serial.print(out);
  //Serial.println();

  if (armed) {
    u8g.setColorIndex(1);
    u8g.drawBox(0, 0, 46, 18);
    u8g.setColorIndex(0);
    u8g.drawStr(1,16, "ARM");
    u8g.setColorIndex(1);
  } else {
    u8g.setColorIndex(0);
    u8g.drawBox(0, 0, 46, 18);
    u8g.setColorIndex(1);
    u8g.drawStr(1,16, "SAFE");
  }
}

void draw(void) {
  if (millis() < 3000) {
    u8g.drawXBMP(32, 0, fablab_width, fablab_height, fablab_bits);
  } else {
    u8g.setColorIndex(1);
    drawLogo(0);
    drawStatus(bArm);
    drawURL();
  }
}

void setup(void) {
  //u8g.setRot180();   // flip screen, if required
  Serial.begin(115200);
}

void loop(void) {
  // picture loop
  if (millis() > ms1 + 500) {
    ms1 = millis();
    // rebuild the picture after some delay
    u8g.firstPage();  
    do {
      draw();
      u8g.setColorIndex(1);
    } while( u8g.nextPage() );
  }
 

  if (millis() > ms + 2000) {
    ms = millis();
    bArm = !bArm;
  }
}

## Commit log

2019-06-02 Change pin assignment for Fabbot
2019-06-04 Fix motional speed and some bindings
    [mini_turty3.cpp]
2019-12-05 Added sources
    [fab-turty-base.dxf, fab-turty-motor-holder-x2.dxf, fab-turty-upper.dxf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]

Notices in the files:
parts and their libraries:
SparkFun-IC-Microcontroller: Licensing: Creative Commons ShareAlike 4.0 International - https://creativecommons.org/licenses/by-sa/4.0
